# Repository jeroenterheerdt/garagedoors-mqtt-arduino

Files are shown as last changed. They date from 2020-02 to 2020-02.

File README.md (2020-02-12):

# garagedoors-mqtt-arduino
An alternative to [OpenGarage](https://opengarage.io) that uses ultrasonic sensors to send status of garage doors over MQTT and controls relays to open/close doors. It can be integrated in [Home Assistant](https://home-assistant.io) or any other home automation platform that supports MQTT. Can be extended to more than two doors.

Since OpenGarage only supports one door per install and I had trouble with [ESPHome](https://esphome.io) to work with my two sensors consistently, I decided to create my own. The Arduino ESP8266 sketch in this repo allows you to build a solution that will send the status of two ultrasonic sensors over MQTT (which can be translated to the status of the garage doors in the consuming application, not included in this solution). Also, this sketch receives commands through MQTT and toggles relays to open/close the doors.

## Hardware
- Wemos D1 Mini. You can use any equivalent but you will most likely have to update the code to match the pins.
- US-100 or HC-SR04 ultrasonic sensors, one per door. This sketch assumes two (two doors). If using US-100 make sure to remove the jumper on the sensor.
- Relays, either the Wemos D1 Mini relay shield (I used the relay shield for the right door) or any other 5v/3v relay (I used a general relay for the left door). This sketch assumes two (two garage door controllers).

## Wiring
See the image below and [the Fritzing diagram](double%20garagedoor%20Arduino.fzz). If you like to read instead of looking at an image (who would?) - here is the list of connections to make:
- Wemos 3V --> VCC of ultrasonic sensors (2x)
- Wemos GND --> GND of ultrasonic sensors (2x)
- Wemos GND --> GND of relays (2x)
- Wemos 5V --> VCC of relays (2x)
- Wemos D1 --> D1 of relay 1 (right door)
- Wemos D2 --> SIG of relay 2 (left door)
- Wemos D5 --> echo/rx of ultrasound (right door)
- Wemos D6 --> trigger of ultrasound (right door)
- Wemos D7 --> echo/rx of ultrasound (left door)
- Wemos D8 --> trigger of ultrasound (left door)

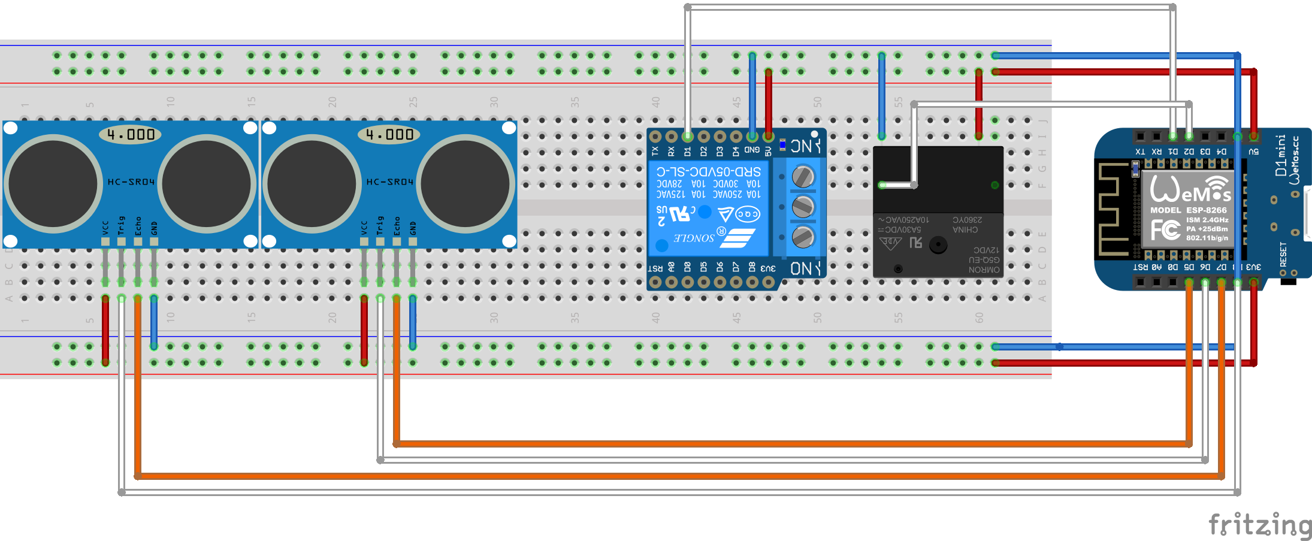
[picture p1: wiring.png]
Wiring diagram


## Software
[The sketch](GarageDoorsArduino.ino) supports over-the-air (OTA), but you will first 'prime' your chip with the OTA software as instructed here [Arduino OTA](https://arduino-esp8266.readthedocs.io/en/latest/ota_updates/readme.html). After that you can deploy this sketch and any updates OTA.

### Requirements
- [Arduino_JSON](https://github.com/arduino-libraries/Arduino_JSON)
- [HCSR04](https://github.com/gamegine/HCSR04-ultrasonic-sensor-lib)
- [ESP8266WiFi](https://arduino-esp8266.readthedocs.io/en/latest/esp8266wifi/readme.html)
- [PubSubClient](https://pubsubclient.knolleary.net/)
- [ArduinoOTA](https://github.com/esp8266/Arduino/tree/master/libraries/ArduinoOTA)

### Configuration

You will probably need to make the following edits in the sketch:
|Line | Setting | Default|
| --- | --- | --- |
|13|configure the hostname you want your esp8266 to have on your network|garagedoors|
|14|configure the password you will use when uploading updates using OTA|password|
|18/19|configure the pin (trigger pin, echo pin) for your ultrasonic sensors. Two have been provided, add more here if you need them|12,14 and 15,13|
|22|time in seconds between each update of sensor status on MQTT|30 seconds|
|27|Your WiFi SSIS|MyWiFi|
|28|Your WiFi security key|NotSecure|
|35|The IPAddress of your MQTT server, with components separated by ',' instead of '.'|192,168,1,2|
|38|The user to login to the MQTT server|user|
|39|The password to login to the MQTT server|password|
|40|The topic you will receive commands on. Command is expected to look like: ```{"door": "left","command":"open"}``` and needs to be valid JSON. `door = left` will map to the left garage door, `door = right` to the right one. `command = open` will open the door, `command = close` will close the door. command is ignored since we only need to know which relay (door) to toggle this assumes you will never send a command while the door is still in motion. |garagedoors/command|
|42/43|The topics two write the sensor status to, one per door. Two have been provided, add more here if you need them.|garagedoors/right, garagedoors/left|
|50/51|The pins for your relays. Two have been provided, add more here if you need them.|D1,D2|
|56|Duration (in milliseconds) to close the switch on the door opener. This should be long enough for the mechanism to start; typically it doesn't to remain activated for the door to complete its motion. It is the same as the time you'd hold down the button to start the door moving.|600|
|105-112|Add more if/else if/else constructs if you need to control more than two doors|N/A|
|190/191|Add initialization of more relay pins if you need to control more than two doors|N/A|
|215-220|Add code to read and publish ultrasonic sensor readings in the corresponding MQTT topics if you need to control more than two doors|N/A|

## Home Assistant configuration
Since I kept the work in the Arduino sketch to a minimum as possible there are quite some things to configure in Home Assistant. This is my config (all for two doors):
```yaml
input_number: #these are used to make the state switching configurable in the UI
  garage_door_closed_distance_setting: 
      name: Garage Door Closed Distance Setting
      min: 0
      max: 1000
      step: 1
      mode: box
  garage_door_vehicle_present_distance_setting:
      name: Garage Door Vehicle Present Distance Setting
      min: 0
      max: 1000
      step: 1
      mode: box
sensor:
  - platform: mqtt
    name: Garage Door Distance Left
    state_topic: "garagedoors/left"
    icon: mdi:altimeter
    unit_of_measurement: cm
  - platform: mqtt
    name: Garage Door Distance Right
    state_topic: "garagedoors/right"
    icon: mdi:altimeter
    unit_of_measurement: cm
  - platform: template
    sensors:
      garagedoor_left_state:
        friendly_name: Left Garage Door State
        value_template: "{%if states('sensor.garage_door_distance_left')|float < states('input_number.garage_door_closed_distance_setting')|float %} Closed {% elif states('sensor.garage_door_distance_left')|float < states('input_number.garage_door_vehicle_present_distance_setting')|float %} Vehicle Present {% else %} Open {% endif %}"
        icon_template: "{%if states('sensor.garage_door_distance_left')|float < states('input_number.garage_door_closed_distance_setting')|float %} mdi:garage {% elif states('sensor.garage_door_distance_left')|float < states('input_number.garage_door_vehicle_present_distance_setting')|float %} mdi:garage-alert {% else %} mdi:garage-open {% endif %}"
      garagedoor_right_state:
        friendly_name: Right Garage Door State
        value_template: "{%if states('sensor.garage_door_distance_right')|float < states('input_number.garage_door_closed_distance_setting')|float %} Closed {% elif states('sensor.garage_door_distance_right')|float < states('input_number.garage_door_vehicle_present_distance_setting')|float %} Vehicle Present {% else %} Open {% endif %}"
        icon_template: "{%if states('sensor.garage_door_distance_right')|float < states('input_number.garage_door_closed_distance_setting')|float %} mdi:garage {% elif states('sensor.garage_door_distance_right')|float < states('input_number.garage_door_vehicle_present_distance_setting')|float %} mdi:garage-alert {% else %} mdi:garage-open {% endif %}"
cover:
  - platform: template
    covers:
      garage_door_left:
        friendly_name: Garage Door Left
        value_template: "{{ is_state('sensor.garagedoor_left_state','Open')}}"
        open_cover:
          service: mqtt.publish
          data:
            topic: garagedoors/command
            payload: '{"door":"left", "command":"open"}'
            retain: false
        close_cover:
          service: mqtt.publish
          data:
            topic: garagedoors/command
            payload: '{"door":"left", "command":"close"}'
            retain: false
        stop_cover: 
          service: mqtt.publish
          data:
            topic: garagedoors/command
            payload: '{"door":"left", "command":"stop"}'
            retain: false
      garage_door_right:
        friendly_name: Garage Door Right
        value_template: "{{ is_state('sensor.garagedoor_right_state','Open')}}"
        open_cover:
          service: mqtt.publish
          data:
            topic: garagedoors/command
            payload: '{"door":"right", "command":"open"}'
            retain: false
        close_cover:
          service: mqtt.publish
          data:
            topic: garagedoors/command
            payload: '{"door":"right", "command":"close"}'
            retain: false
        stop_cover: 
          service: mqtt.publish
          data:
            topic: garagedoors/command
            payload: '{"door":"right", "command":"stop"}'
            retain: false
```

In the UI, these are the cards that I added:

Left door:
```yaml
entities:
  - entity: cover.garage_door_left
  - entity: sensor.garagedoor_left_state
  - entity: sensor.garage_door_distance_left
show_header_toggle: false
title: Left Garage Door
type: entities
```

Right door:
```yaml
entities:
  - entity: cover.garage_door_right
  - entity: sensor.garagedoor_right_state
  - entity: sensor.garage_door_distance_right
show_header_toggle: false
title: Right Garage Door
type: entities

```

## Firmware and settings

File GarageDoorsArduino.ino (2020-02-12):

#include <Arduino_JSON.h>
#include <HCSR04.h>
#include <ESP8266WiFi.h>
#include <PubSubClient.h>
#include <stdio.h>
#include <ArduinoOTA.h>

//--------------
//SETUP / CONFIG
//--------------

//OTA
const char* hostname = "garagedoors";
const char* ota_pass = "password";

//ULTRASOUND SENSORS
//this is for two garagedoors, add more here if you need them.
HCSR04 hc_right(12,14);//initialisation class HCSR04 (trig pin , echo pin)
HCSR04 hc_left(15,13); //(trigger,echo)

//LOOP TIMER
int wait_seconds= 30; //number of seconds between statusupdated from your ultrasound sensors
unsigned long time_now = 0;

// WIFI
#ifndef STASSID
#define STASSID "MyWiFi"
#define STAPSK "NotSecure"
#endif

const char* ssid = STASSID;
const char* password = STAPSK;

//MQTT
IPAddress server(192,168,1,2); //mqtt server IP
WiFiClient wclient;
PubSubClient client(wclient, server);
const char* mqttuser = "user";
const char* mqttpass = "password";
const char* inTopic = "garagedoors/command"; //topic to subscribe to to receive commands
//outtopics for two garagedoors, add more here if you need them.
const char* outTopicR = "garagedoors/right";
const char* outTopicL = "garagedoors/left";
char temp[10]; //enough to store 2 decimals, a decimal seperator and 7 digits for up to 1000000 meters (not that your sensor will reach that far).
char payload_str[35]; //exactly 35 characters max payload
JSONVar payload_json;

//RELAYS
//this defines two relays for two doors, add more here if you need them
const int relayPinR = D1; // relay for the right door is on D1
const int relayPinL = D2; // relay for the left door is on D2
// Duration to close the switch on the door opener. This should be long
// enough for the mechanism to start; typically it doesn't to remain 
// activated for the door to complete its motion. It is the same as the
// time you'd hold down the button to start the door moving. 
const int relayActivationPeriod = 600; //ms

//-------
//METHODS
//-------
//this is called in the callback to toggle a pin to high, wait and then to low
void toggle(int pin) {
  Serial.print(F("Toggling pin: "));
  Serial.println(pin);
  digitalWrite(pin,HIGH);
  delay(relayActivationPeriod);
  digitalWrite(pin,LOW);
}

//MQTT callback
//the code assumes a JSON: {"door": "left","command":"open"}
//door = left will map to the left garage door, door = right to the right one
//commands = open will open the door, command = close will close the door
//command is ignored since we only need to know which relay (door) to toggle
//this assumes you will never send a command while the door is still in motion. 
void callback(const MQTT::Publish& pub) {
  // handle message arrived
  Serial.print(pub.topic());
  Serial.print(" => ");
  /*if (pub.has_stream()) {
    Serial.println("stream");
    uint8_t buf[BUFFER_SIZE];
    int read;
    while (read = pub.payload_stream()->read(buf, BUFFER_SIZE)) {
      Serial.write(buf, read);
    }
    pub.payload_stream()->stop();
    Serial.println("");
  } else*/
  Serial.println(pub.payload_string());
  
  payload_json = JSON.parse(pub.payload_string());
  if (JSON.typeof(payload_json) == "undefined") {
    Serial.println(F("Parsing input failed!"));
    return;
  }
  else {
    if(payload_json.hasOwnProperty("door")) {
      Serial.print(F("Payload door: "));
      Serial.println(payload_json["door"]);
      //Serial.print(F("Payload command: "));
      //Serial.println(payload_json["command"]);
      
      //this if/else handles two doors, add more else statements if you need them.
      if(strcmp(payload_json["door"],"left")==0) {
      //toggle left relay
        toggle(relayPinL);
      }
      else if(strcmp(payload_json["door"],"right")==0) {
        //toggle right relay
        toggle(relayPinR);
      }
     }
  }
}

void connectMQTT() {
  Serial.println(F("Connecting to MQTT server"));
  if (client.connect(MQTT::Connect("arduinoClient")
     .set_auth(mqttuser, mqttpass))) {
     Serial.println(F("Connected to MQTT server"));
     client.set_callback(callback);
     client.subscribe(inTopic);  
  } else {
     Serial.println(F("Could not connect to MQTT server"));  
  }
}

void setup()
{ Serial.begin(115200); 
  // Connect to WiFi network
  Serial.println();
  Serial.println();
  Serial.print(F("Connecting to "));
  Serial.println(ssid);

  WiFi.mode(WIFI_STA);
  WiFi.begin(ssid, password);

  while (WiFi.status() != WL_CONNECTED) {
    delay(500);
    Serial.print(F("."));
  }
  Serial.println();
  Serial.println(F("WiFi connected"));
  Serial.println(WiFi.localIP());
 
  if (!client.connected()) {
      connectMQTT();
  }

  //OTA
  ArduinoOTA.setHostname(hostname);
  ArduinoOTA.setPassword(ota_pass);
  ArduinoOTA.onStart([]() {
    String type;
    if (ArduinoOTA.getCommand() == U_FLASH) {
      type = "sketch";
    } else { // U_FS
      type = "filesystem";
    }

    // NOTE: if updating FS this would be the place to unmount FS using FS.end()
    Serial.println("Start updating " + type);
  });
  ArduinoOTA.onEnd([]() {
    Serial.println("\nEnd");
  });
  ArduinoOTA.onProgress([](unsigned int progress, unsigned int total) {
    Serial.printf("Progress: %u%%\r", (progress / (total / 100)));
  });
  ArduinoOTA.onError([](ota_error_t error) {
    Serial.printf("Error[%u]: ", error);
    if (error == OTA_AUTH_ERROR) {
      Serial.println(F("Auth Failed"));
    } else if (error == OTA_BEGIN_ERROR) {
      Serial.println(F("Begin Failed"));
    } else if (error == OTA_CONNECT_ERROR) {
      Serial.println(F("Connect Failed"));
    } else if (error == OTA_RECEIVE_ERROR) {
      Serial.println(F("Receive Failed"));
    } else if (error == OTA_END_ERROR) {
      Serial.println(F("End Failed"));
    }
  });
  ArduinoOTA.begin();

  //Relays
  //add more here if you have more than 2 relays defined (more than two doors)
  pinMode(relayPinR,OUTPUT);digitalWrite(relayPinR,LOW);
  pinMode(relayPinL,OUTPUT);digitalWrite(relayPinL,LOW);
}

//this is called from the loop() for each garagedoor sensor.
void publishReading(const char* theTopic, float reading) {
  dtostrf(reading,6,2,temp);
  Serial.print(F("Publishing: " ));
  Serial.print(theTopic);
  Serial.print(F(" => "));
  Serial.println(temp);
  client.publish(theTopic,temp); //publish
}

void loop()
{ 
  //OTA
  ArduinoOTA.handle();
  
  //CONNECT TO MQTT
  if(client.connected()) {
    if(millis() > time_now + (wait_seconds*1000)) {
      time_now = millis();
      
      //this is for two garagedoors, add more here if you need them.
      Serial.print(F("reading right: "));
      Serial.println(hc_right.dist());
      Serial.print(F("reading left: "));
      Serial.println(hc_left.dist());
      publishReading(outTopicR,hc_right.dist()); //publish reading for right garagedoor
      publishReading(outTopicL,hc_left.dist()); //publish reading for left garagedoor
   }
        
    client.loop();
  }
  else {
    connectMQTT();
  }
  
}
